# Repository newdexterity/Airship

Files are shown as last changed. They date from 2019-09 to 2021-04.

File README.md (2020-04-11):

# A Low-Cost, Open-Source, Robotic Airship for Education and Research

Miniature indoor robotic airship platforms offer high mobility, safety, and extended flight times. The work focuses on the feasibility, design, development, and evaluation of such a platform for robotics education and research. Selected commercially available envelope materials were considered and tested in terms of their helium retention capability. The obtained envelope properties were used in a feasibility study, demonstrating that indoor airships are environmentally and financially viable, given an appropriate material choice. The platform's mechanical design was studied in terms of gondola placement and rotor angle positioning, resulting in an unconventional, asymmetric arrangement. The developed system was finally tested in a simple path following experiment for proof-of-concept purposes, proving its efficiency in attaining the desired heading and altitude configuration. The proposed robotic airship platform can be used for a variety of education and research oriented applications and its design is open-source facilitating replication by others.

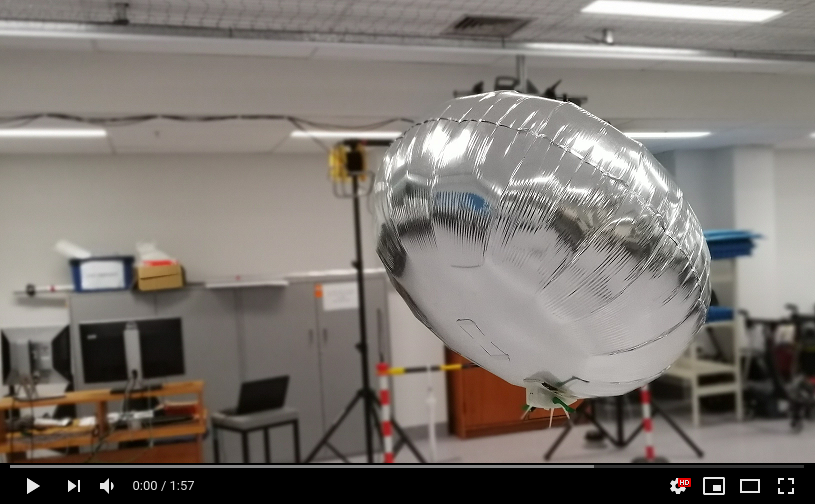
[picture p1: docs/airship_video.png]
Airship video (https://youtu.be/TQCl9RjmE-4)


## Repository Contents
This repository contains the following material:
* Assembly guide and bill of materials
* CAD files of the airship platform
* ROS interface for flight control and path following

## Gondola Design
The airship gondola is built around the electronic components and actuators listed in the provided bill of materials.
The central control and communication unit is a Raspberry Pi Zero W running a Lite version of the Raspbian Stretch operating system. 
Peripheral components include a single cell 500 mAh Li-Ion battery, step-up voltage regulator, motor drivers, three 7x16 mm DC motors, three 57x20 mm propeller units and a camera module that will facilitate the formulation of HRI frameworks.
Rotor speeds can either be controlled by on-board logic or manually via a wireless connection through SSH or an appropriately developed Robot Operating System (ROS) package.
The combined cost of the gondola components (excluding the 3D printing filament and wiring) comes to 90 USD, which drops to 54 USD if the camera module is not required.
The physical frame is 3D printed and built in a modular fashion: the gondola legs and rotor brackets are detachable to facilitate component modification and replacement.
The gondola is attached to the chosen envelope using Velcro.
The assembled gondola and its exploded view model are presented below:
<p align="center">
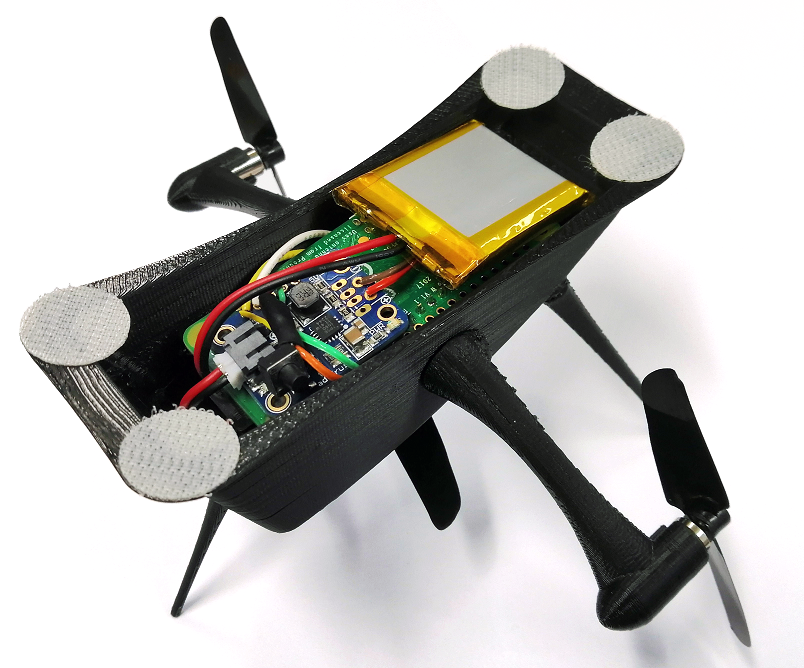
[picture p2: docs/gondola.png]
  
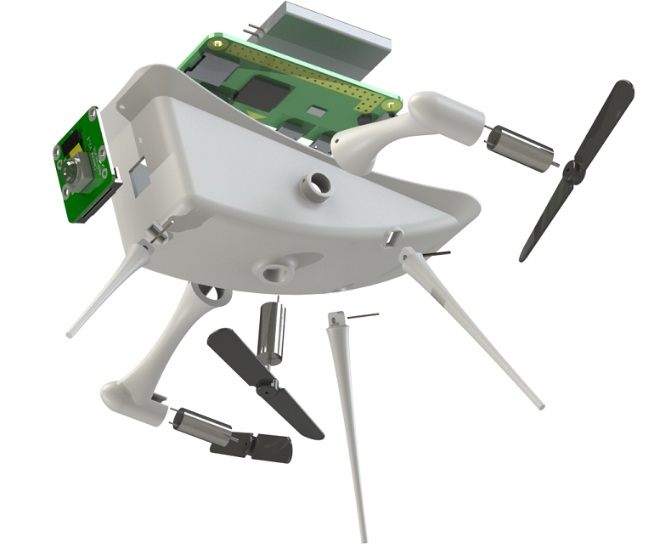
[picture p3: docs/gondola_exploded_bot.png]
  
</p>

## Envelope Material
A number of envelope material candidates were examined with respect to their helium permeability and mechanical properties:
* Qualatex untreated round 41 cm (16 inch) latex balloon
* Qualatex untreated round 61 cm (24 inch) latex balloon
* Qualatex round 61 cm (24 inch) latex balloon treated with Ultra Hi-Float (UHF) \cite{HiFloatPatent}
* Qualatex 61 cm (24 inch) clear Bubble balloon (layered membrane including a high barrier layer of ethylene vinyl alcohol copolymer)
* Qualatex round 91 cm (36 inch) Microfoil (metallised PET) balloon

<p align="center">
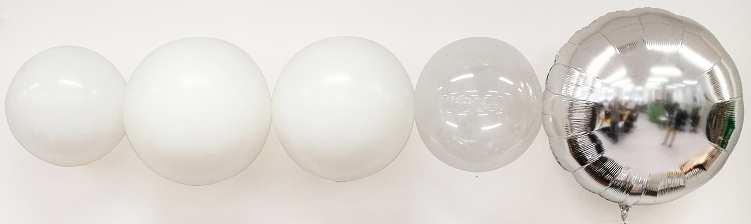
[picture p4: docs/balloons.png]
  
</p>

The daily helium flux through balloon membranes was computed:
<p align="center">
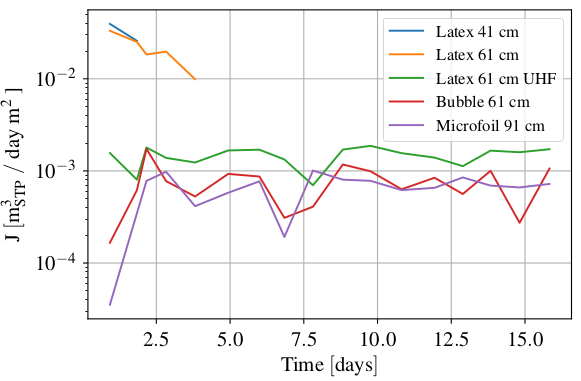
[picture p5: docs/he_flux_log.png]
  
</p>

The average helium flux values and yearly refill costs for different envelope materials:
<p align="center">
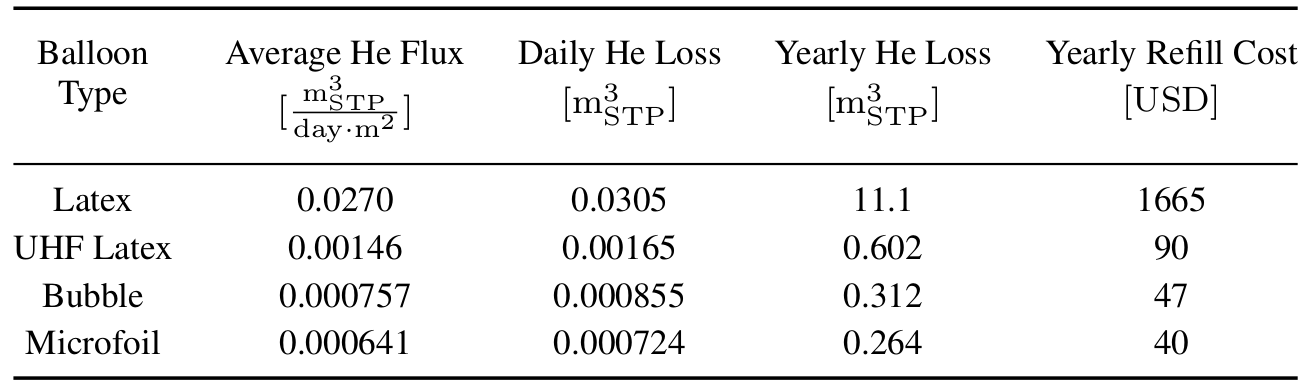
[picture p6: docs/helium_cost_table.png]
  
</p>

The measured mechanical properties of latex, Microfoil and Bubble membranes:
<p align="center">
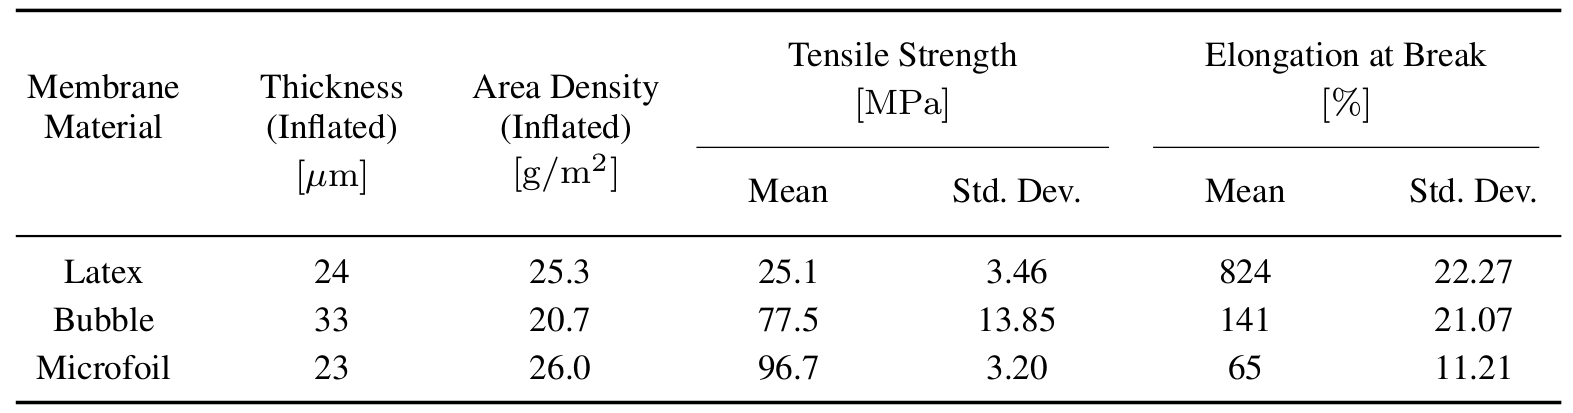
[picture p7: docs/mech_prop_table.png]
  
</p>

## Path Following
The airship was evaluated in terms of its path following ability in an indoor environment.
Path following was implemented using a discrete variation of the carrot-chasing algorithm, where the desired path is segmented into a sequence of waypoints.
In a given location, the airship identifies its position with respect to desired path and directs itself towards an appropriate waypoint:

<p align="center">
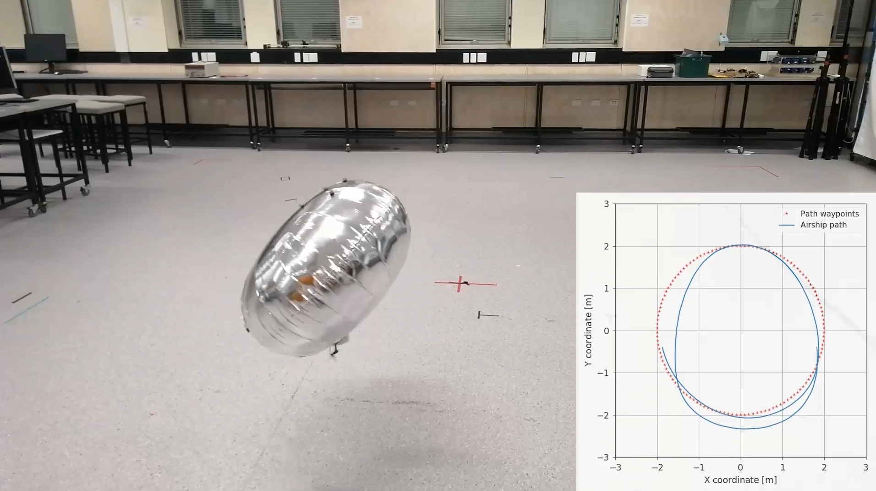
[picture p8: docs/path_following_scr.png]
  
</p>

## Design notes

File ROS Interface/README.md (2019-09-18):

# airshippi_vicon

Example ROS interface to use with the Vicon motion capture system. 
The package relies on the pigpio library: http://abyz.me.uk/rpi/pigpio/ and the vicon_bridge ROS package.

## Usage

The pigpio_setter.py node should be run on the raspberry pi, while others are examples of closed loop flight controllers.

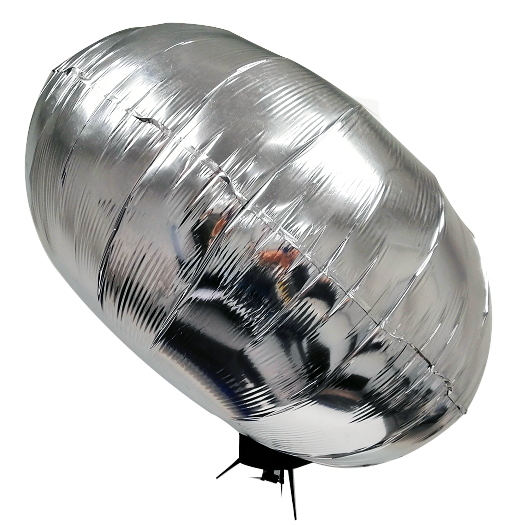
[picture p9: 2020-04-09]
docs/gondola_offset.png

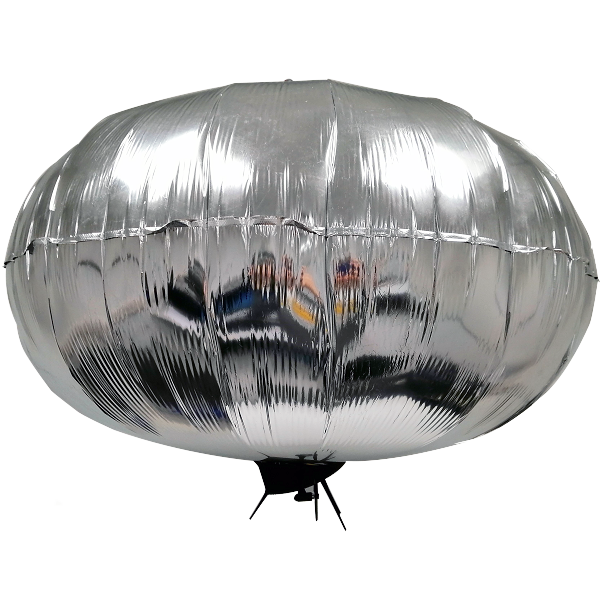
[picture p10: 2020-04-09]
docs/gondola_centred.png

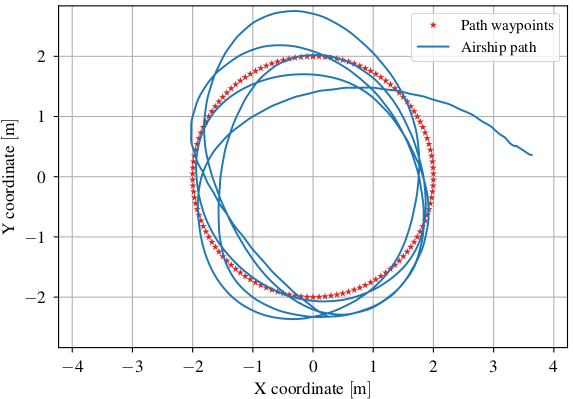
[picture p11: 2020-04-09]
docs/pf_circle.png

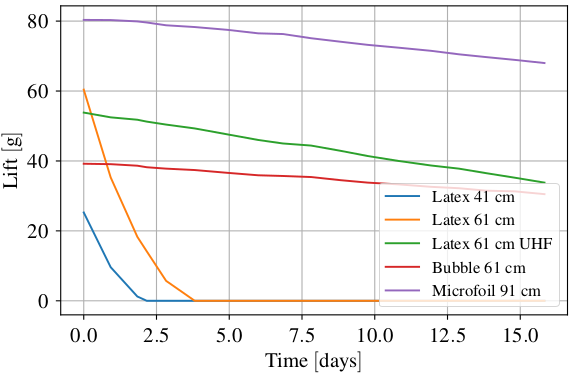
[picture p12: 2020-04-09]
docs/raw_lift.png

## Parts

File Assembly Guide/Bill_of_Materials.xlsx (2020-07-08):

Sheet: USA
PRODUCT NUMBER | DESCRIPTION | QUANTITY | INDIVIDUAL PRICE | COMBINED PRICE | COMPANY | RESELLER COMPANY | LINK TO RESELLER WEBPAGE | ALT LINKS | ADDITIONAL INFO
3400 | Raspberry Pi Zero W | 1 | 10 USD | 10 USD | AdaFruit | AdaFruit | https://www.adafruit.com/product/3400
1578 | Lithium Ion Polymer Battery - 3.7v 500mAh | 1 | 7.95 USD | 7.95 USD | AdaFruit | AdaFruit | https://www.adafruit.com/product/1578
1903 | PowerBoost 500 Basic - 5V USB Boost @ 500mA from 1.8V+ | 1 | 9.95 USD | 9.95 USD | Adafruit | Adafruit | https://www.adafruit.com/product/1903
2135 | DRV8835 Dual Motor Driver Carrier | 1 | 4.49 USD | 4.49 USD | Pololu | Pololu | https://www.pololu.com/product/2135
2990 | DRV8838 Single Brushed DC Motor Driver Carrier | 1 | 3.49 USD | 3.49 USD | Pololu | Pololu | https://www.pololu.com/product/2990
/ | Motor-7x16mm 3.3Ohm w/nanoconnector | 3 | 4.29 USD | 12.87 USD | Plantraco MicroFlight | AliExpress | https://www.aliexpress.com/item/32957638292.html | http://microflight.com/radio-systems/motors/motor-7mm-3-3ohm-w-nanoconnector.html | Micro motor, brushed, width 7mm, length 16.5mm, voltage 3.7 V, resistance 3.3 Ohm
/ | Propeller 57x20 mm | 3 | 1.49 USD | 4.47 USD | Plantraco MicroFlight | Plantraco MicroFlight | http://microflight.com/radio-systems/propellers/prop-57x20-for-1mm-shaft.html
3099 | Raspberry Pi Camera Board v2 - 8 Megapixels | 1 | 29.95 USD | 29.95 USD | AdaFruit | AdaFruit | https://www.adafruit.com/product/3099
3157 | Raspberry Pi Zero v1.3 Camera Cable | 1 | 5.95 USD | 5.95 USD | AdaFruit | AdaFruit | https://www.adafruit.com/product/3157
12683 | Qualatex Round Microfoil Balloon: 36’’ Silver | 1 | ~2.5 USD | ~2.5 USD | Qualatex | Refer to Alt Link | https://us.qualatex.com/en-us/products/12683/?product_type=Qualatex%20Foil%20Balloons | https://us.qualatex.com/en-us/products/12683/?product_type=Qualatex%20Foil%20Balloons

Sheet: Europe
PRODUCT NUMBER | DESCRIPTION | QUANTITY | INDIVIDUAL PRICE | COMBINED PRICE | COMPANY | RESELLER COMPANY | LINK TO RESELLER WEBPAGE | ALT LINK
3400 | Raspberry Pi Zero W | 1 | 10 USD | 10 USD | AdaFruit | AdaFruit | https://www.adafruit.com/product/3400
1578 | Lithium Ion Polymer Battery - 3.7v 500mAh | 1 | 7.95 USD | 7.95 USD | AdaFruit | AdaFruit | https://www.adafruit.com/product/1578
1903 | PowerBoost 500 Basic - 5V USB Boost @ 500mA from 1.8V+ | 1 | 9.95 USD | 9.95 USD | Adafruit | Adafruit | https://www.adafruit.com/product/1903
2135 | DRV8835 Dual Motor Driver Carrier | 1 | 4.49 USD | 4.49 USD | Pololu | Pololu | https://www.pololu.com/product/2135
2990 | DRV8838 Single Brushed DC Motor Driver Carrier | 1 | 3.49 USD | 3.49 USD | Pololu | Pololu | https://www.pololu.com/product/2990
/ | Motor-7mm 3.3Ohm w/nanoconnector | 3 | 4.29 USD | 12.87 USD | Plantraco MicroFlight | Plantraco MicroFlight | http://microflight.com/radio-systems/motors/motor-7mm-3-3ohm-w-nanoconnector.html
/ | Prop-57x20 for 1mm Shaft | 3 | 1.49 USD | 4.47 USD | Plantraco MicroFlight | Plantraco MicroFlight | http://microflight.com/radio-systems/propellers/prop-57x20-for-1mm-shaft.html
3099 | Raspberry Pi Camera Board v2 - 8 Megapixels | 1 | 29.95 USD | 29.95 USD | AdaFruit | AdaFruit | https://www.adafruit.com/product/3099
3157 | Raspberry Pi Zero v1.3 Camera Cable | 1 | 5.95 USD | 5.95 USD | AdaFruit | AdaFruit | https://www.adafruit.com/product/3157
12683 | Qualatex Round Microfoil Balloon: 36’’ Silver | 1 | ~2.5 USD | ~2.5 USD | Qualatex | Refer to Alt Link | https://europe.qualatex.com/en-gb/products/12683/?product_type=Qualatex%20Foil%20Balloons | https://europe.qualatex.com/en-gb/purchase-qualatex-balloons/europe-distributors/

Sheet: Asia
PRODUCT NUMBER | DESCRIPTION | QUANTITY | INDIVIDUAL PRICE | COMBINED PRICE | COMPANY | RESELLER COMPANY | LINK TO RESELLER WEBPAGE | ALT LINK
3400 | Raspberry Pi Zero W | 1 | 10 USD | 10 USD | AdaFruit | AdaFruit | https://www.adafruit.com/product/3400
1578 | Lithium Ion Polymer Battery - 3.7v 500mAh | 1 | 7.95 USD | 7.95 USD | AdaFruit | AdaFruit | https://www.adafruit.com/product/1578
1903 | PowerBoost 500 Basic - 5V USB Boost @ 500mA from 1.8V+ | 1 | 9.95 USD | 9.95 USD | Adafruit | Adafruit | https://www.adafruit.com/product/1903
2135 | DRV8835 Dual Motor Driver Carrier | 1 | 4.49 USD | 4.49 USD | Pololu | Pololu | https://www.pololu.com/product/2135
2990 | DRV8838 Single Brushed DC Motor Driver Carrier | 1 | 3.49 USD | 3.49 USD | Pololu | Pololu | https://www.pololu.com/product/2990
/ | Motor-7mm 3.3Ohm w/nanoconnector | 3 | 4.29 USD | 12.87 USD | Plantraco MicroFlight | Plantraco MicroFlight | http://microflight.com/radio-systems/motors/motor-7mm-3-3ohm-w-nanoconnector.html
/ | Prop-57x20 for 1mm Shaft | 3 | 1.49 USD | 4.47 USD | Plantraco MicroFlight | Plantraco MicroFlight | http://microflight.com/radio-systems/propellers/prop-57x20-for-1mm-shaft.html
3099 | Raspberry Pi Camera Board v2 - 8 Megapixels | 1 | 29.95 USD | 29.95 USD | AdaFruit | AdaFruit | https://www.adafruit.com/product/3099
3157 | Raspberry Pi Zero v1.3 Camera Cable | 1 | 5.95 USD | 5.95 USD | AdaFruit | AdaFruit | https://www.adafruit.com/product/3157
12683 | Qualatex Round Microfoil Balloon: 36’’ Silver | 1 | ~2.5 USD | ~2.5 USD | Qualatex | Refer to Alt Link | https://asia.qualatex.com/en-us/products/12683/?product_type=Qualatex%20Foil%20Balloons | https://asia.qualatex.com/en-us/purchase-qualatex-balloons/asia-distributors/

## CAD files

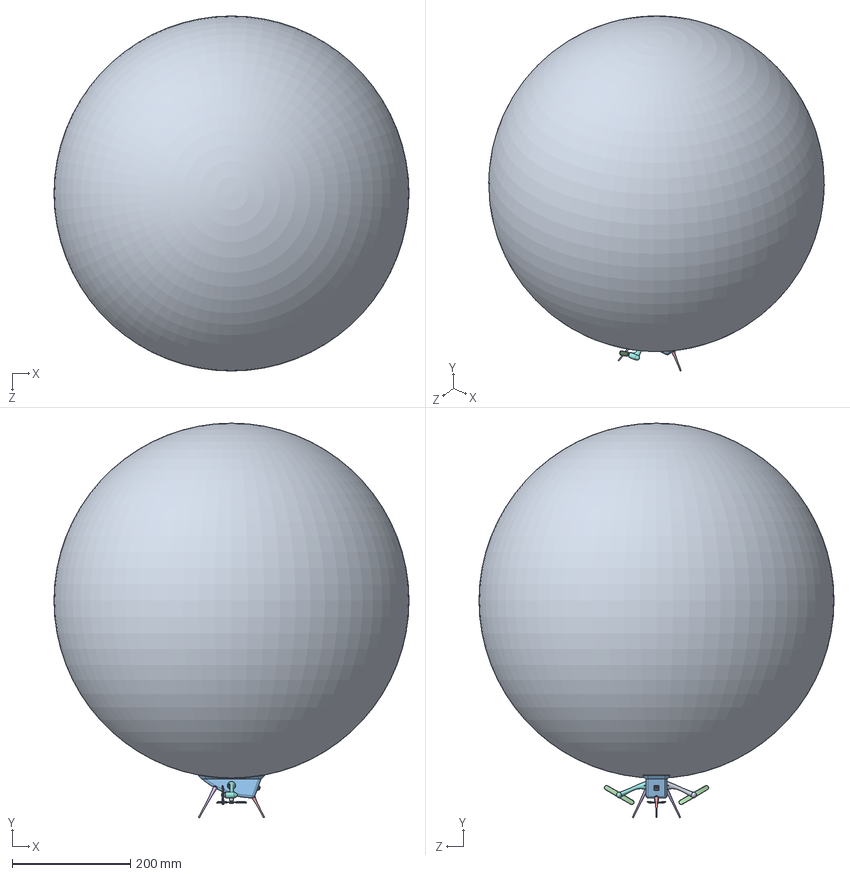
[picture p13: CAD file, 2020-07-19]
CAD/gondola/platform.SLDASM
600.0 x 667.1 x 600.0 mm
RaspberryPiZeroW
PicameraPCB
OVA5647_Housing
OVA5647_Lens_FOV
ribbon_cam
CCD
CAPC-0805-T0.75-BN x 2
CAPC-0402-T0.55-BN x 10
RESC-0402 x 3
RESC-0603 x 2
RESC-1210
c-1-1734248-5-e-raspberry_display
SOT23-5 x 3
KX7 SMD Quartz Crystal Resonator 3.2x2.5mm
c6aaa
4pin_smd x 3
plantraco_7mm_motor x 3
battery_1s_500mah
frame_v3
propeller_57mm x 3
front_leg
back_leg x 2
pinheader_straight x 3
right_wing
left_wing

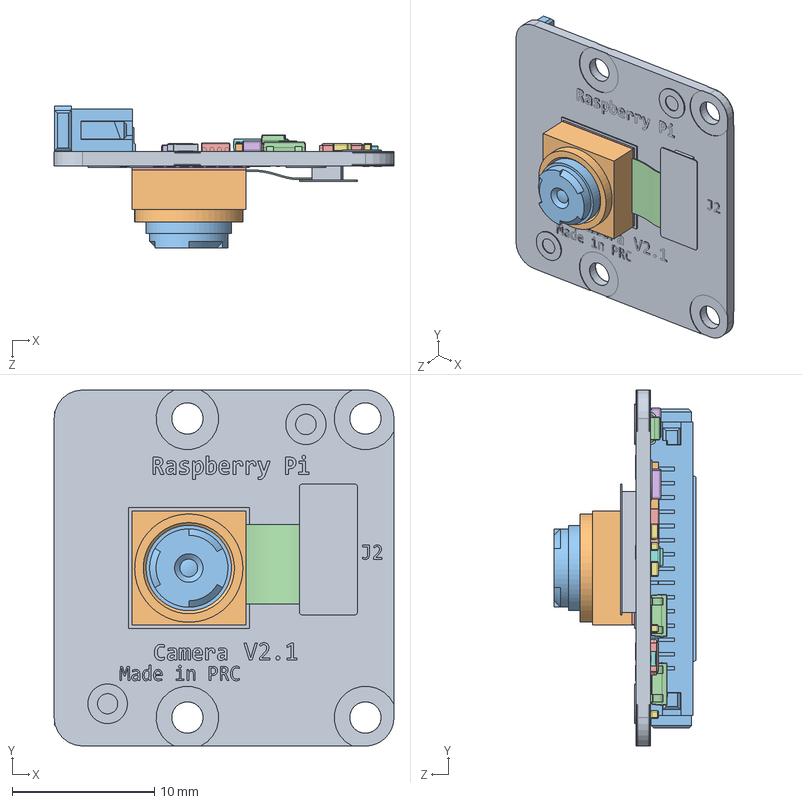
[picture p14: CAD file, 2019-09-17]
CAD/parts/RaspberryPiCameraModuleV2/RspCameraMia.SLDASM
23.9 x 25.0 x 9.96 mm
PicameraPCB
OVA5647_Housing
OVA5647_Lens_FOV
ribbon_cam
CCD
CAPC-0805-T0.75-BN x 2
CAPC-0402-T0.55-BN x 10
RESC-0402 x 3
RESC-0603 x 2
RESC-1210
c-1-1734248-5-e-raspberry_display
SOT23-5 x 3
KX7 SMD Quartz Crystal Resonator 3.2x2.5mm
c6aaa
4pin_smd x 3

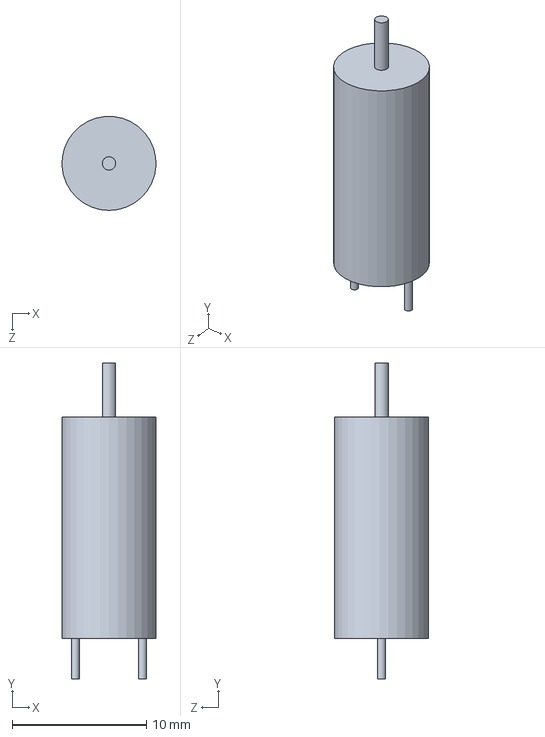
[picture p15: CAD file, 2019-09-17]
CAD/parts/plantraco_7mm_motor.SLDPRT
6.99 x 23.5 x 6.98 mm

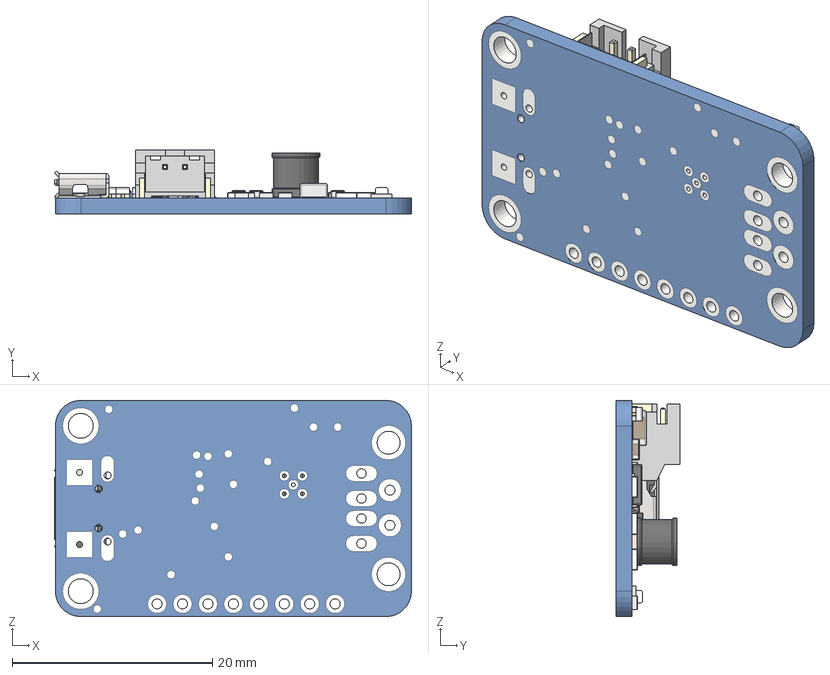
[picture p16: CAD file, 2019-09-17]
CAD/parts/powerboost-500c-1.snapshot.1/PowerBoost 500C v24.step
35.6 x 6.37 x 21.6 mm
MO-229W3030D-1_4000
Molex2pinSMD
RESC-0805 x 14
MicroUSB
CAPC-0805-T0 x 4
LED-0805H1 x 4
pin x 3
TSOP-5 v4
cap
VLC5045

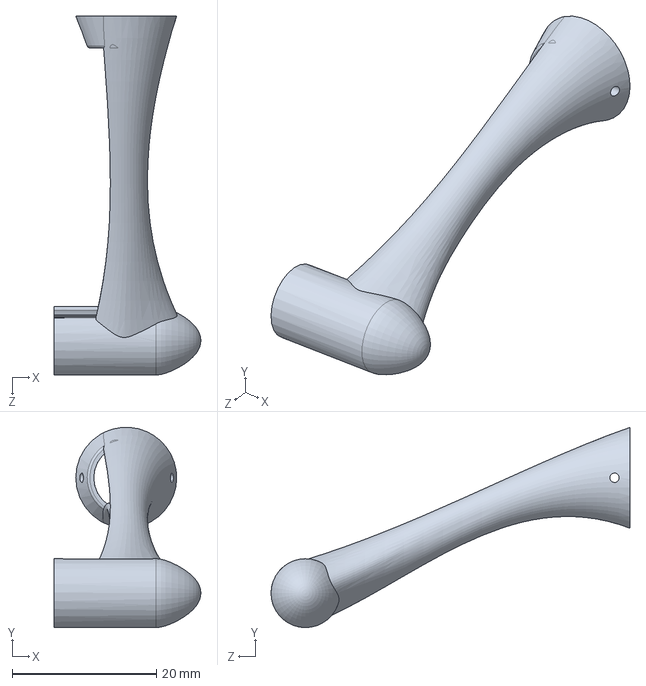
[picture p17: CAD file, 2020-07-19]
CAD/gondola/right_wing.sldprt
20.4 x 27.8 x 49.8 mm

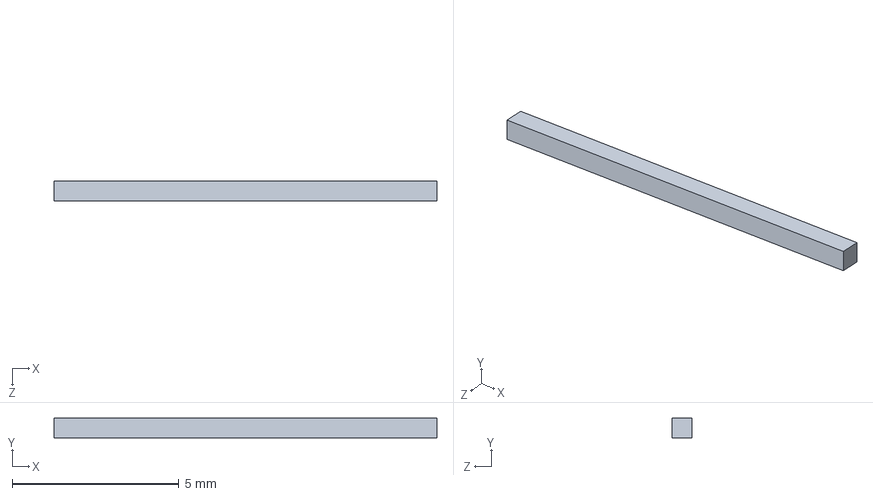
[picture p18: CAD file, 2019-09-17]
CAD/parts/pinheader_straight.SLDPRT
11.5 x 0.6 x 0.6 mm

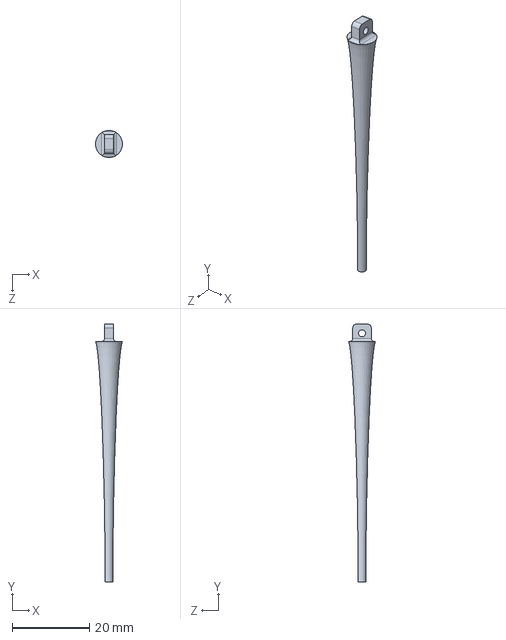
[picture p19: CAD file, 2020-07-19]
CAD/gondola/back_leg.sldprt
6.98 x 66.6 x 6.99 mm

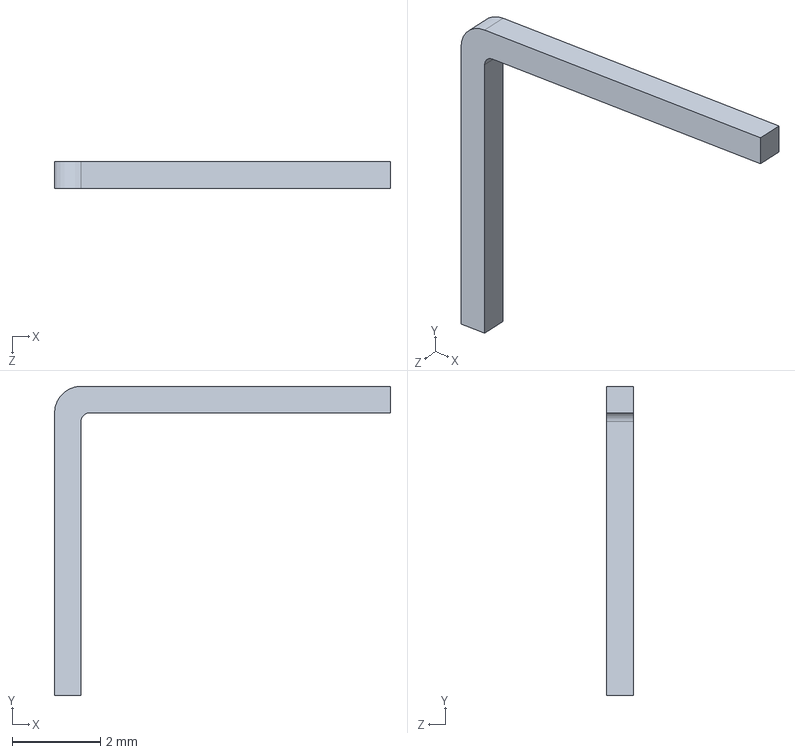
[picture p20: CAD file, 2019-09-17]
CAD/parts/pinheader_bent.SLDPRT
7.60 x 7.00 x 0.6 mm

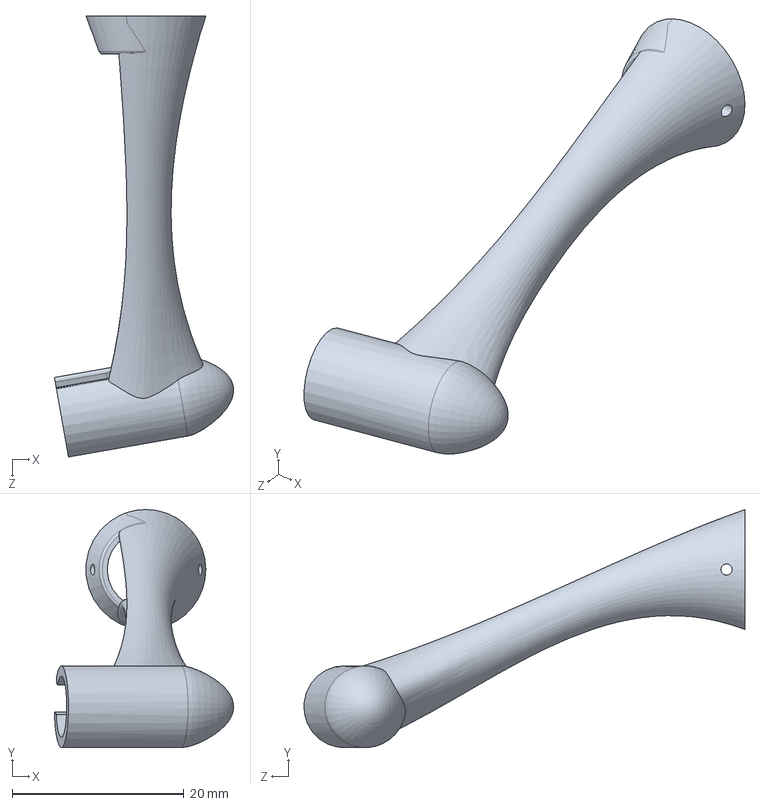
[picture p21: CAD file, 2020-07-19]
CAD/gondola/right_wing_10deg.sldprt
20.9 x 27.8 x 51.4 mm

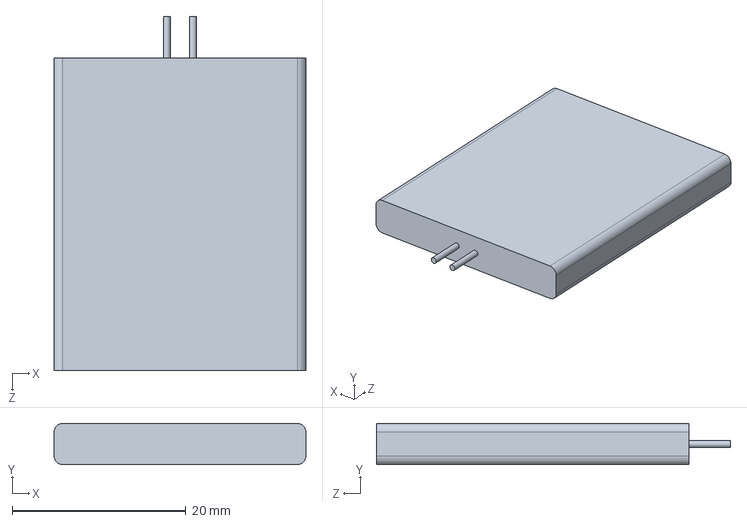
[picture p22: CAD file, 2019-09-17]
CAD/parts/battery_1s_500mah.SLDPRT
29.0 x 4.75 x 40.8 mm

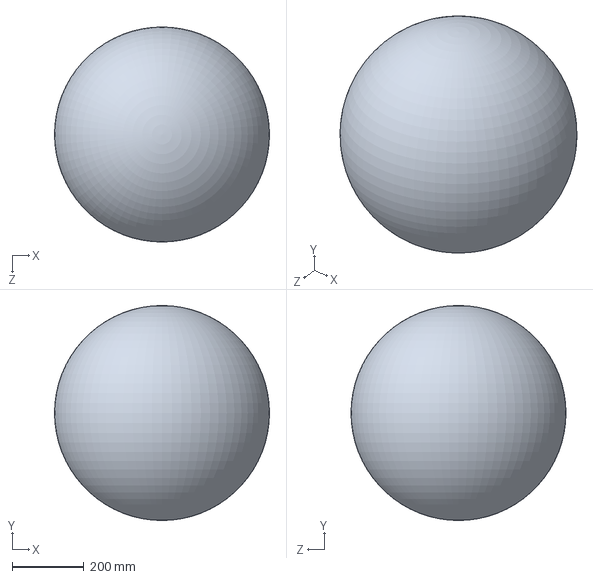
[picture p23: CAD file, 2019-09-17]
CAD/parts/envelope_spherical.SLDPRT
600.0 x 600.0 x 600.0 mm

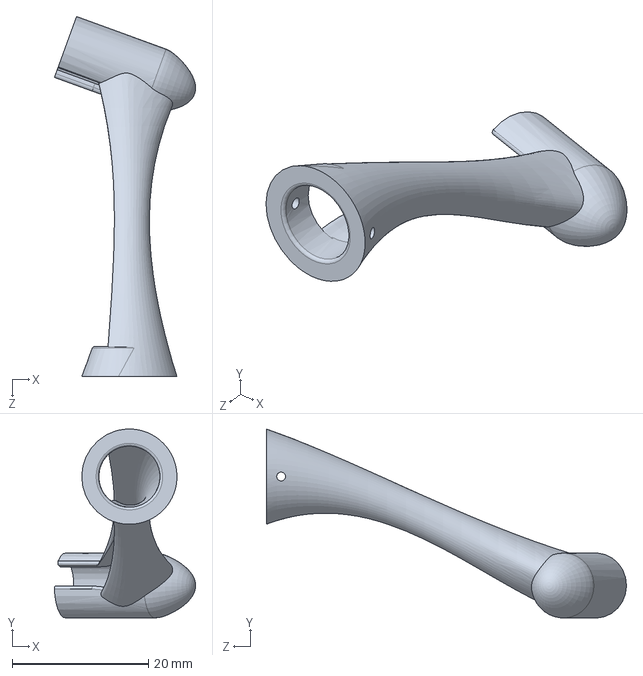
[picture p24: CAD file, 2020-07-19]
CAD/gondola/left_wing_20deg.sldprt
20.8 x 27.8 x 52.9 mm

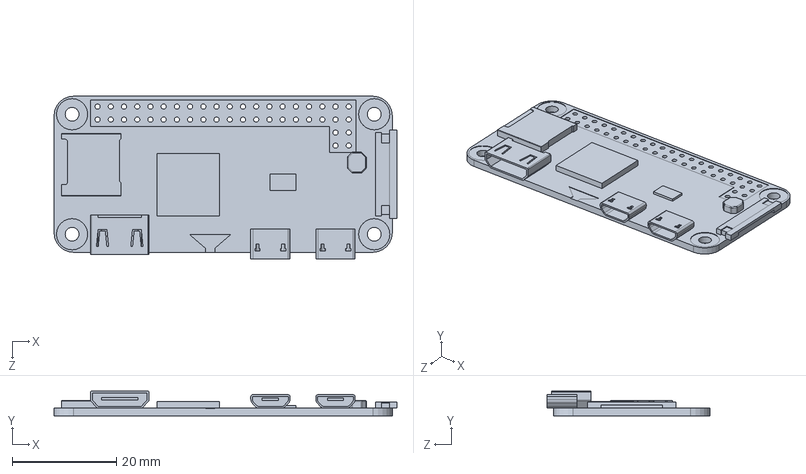
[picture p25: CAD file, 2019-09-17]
CAD/parts/RaspberryPiZeroW.SLDPRT
65.9 x 4.80 x 31.2 mm

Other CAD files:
CAD/parts/RaspberryPiCameraModuleV2/OVA5647_Housing.sldprt
CAD/parts/RaspberryPiCameraModuleV2/CAPC-0805-T0.75-BN.sldprt
CAD/parts/RaspberryPiCameraModuleV2/CCD.sldprt
CAD/gondola/right_wing_5deg.sldprt
CAD/gondola/left_wing.sldprt
CAD/gondola/frame_v3.SLDPRT
CAD/gondola/front_leg.sldprt
CAD/gondola/left_wing_10deg.sldprt
CAD/gondola/left_wing_5deg.sldprt
CAD/gondola/right_wing_20deg.sldprt
CAD/gondola/stl/back_leg.STL
CAD/gondola/stl/frame_v3.STL
CAD/gondola/stl/front_leg.STL
CAD/gondola/stl/left_wing.STL
CAD/gondola/stl/left_wing_10deg.STL
CAD/gondola/stl/left_wing_20deg.STL
CAD/gondola/stl/left_wing_5deg.STL
CAD/gondola/stl/right_wing.STL
CAD/gondola/stl/right_wing_10deg.STL
CAD/gondola/stl/right_wing_20deg.STL
CAD/gondola/stl/right_wing_5deg.STL
CAD/parts/RaspberryPiCameraModuleV2/4pin_smd.sldprt
CAD/parts/RaspberryPiCameraModuleV2/70521906.sldasm
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

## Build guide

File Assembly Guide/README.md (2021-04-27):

# Assembly Guide

## Components
The Bill_of_Materials.xlsx document contains the list of required components to assemble the airship.
It also includes product numbers, prices and links to reseller webpages.

## Motor Driver Connection
The motor drivers can be connected directly to the Raspberry Pi GPIO, as is depicted in the schematic below.
They can be soldered directly to the pins or connected through an appropriate pinheader for easier replacement.
Motor power should be supplied directly from the battery (appropriate pins on the step-up voltage regulator).

<p align="center">
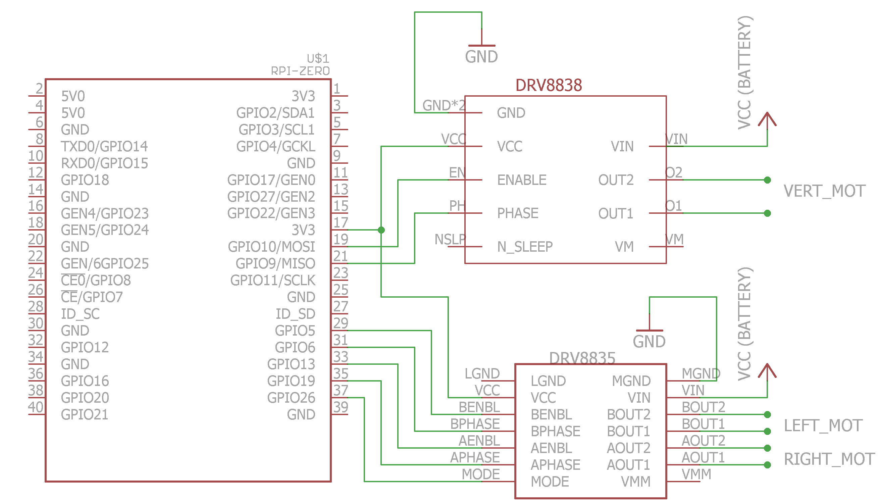
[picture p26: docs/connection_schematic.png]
  
</p>

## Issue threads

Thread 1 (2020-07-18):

Gondola "platform" Solid

marina-go-al, 2020-07-18:
Hello! I am interested in 3d printing the gondola for an educational project using a blimp. However, I have noticed that the "platform" assembly only contains the bottom propeller module and not the ones on the sides (and their corresponding parts/holes), as it appears in the paper. Therefore, I was wondering: could there be something that I am missing?
Thank you very much in advance! (:

gagor15, 2020-07-19:
Hello, thank you for spotting this - some parts were indeed missing.
I've updated the CAD files so everything should be included now: e76559c849d5d8f82b12d201c0d6f98a5627f370

marina-go-al, 2020-07-21:
Perfect, thank you very much, I really appreciate it! Everything looks awesome now

gagor15, 2020-07-21:
Great!

Closed 2020-07-21.

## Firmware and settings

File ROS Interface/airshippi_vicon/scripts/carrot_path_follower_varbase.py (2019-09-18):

#!/usr/bin/env python

## Controls the airship yaw angle

import rospy
import time
import sys
from math import pi, atan2
from geometry_msgs.msg import TransformStamped
from tf.transformations import euler_from_quaternion
from airshippi_vicon.msg import Rotor
from airshippi_vicon.msg import RotorPair
from airshippi_vicon.Path2D import Path, Arc, Line

# ALIGN YAW WITH VICON X AXIS WHEN CREATING OBJECT

# Global params
INVERT_LEFT = True
INVERT_RIGHT = False
RATE_HZ = 5 # Hz
VICON_TOPIC = '/vicon/gal_airship/gal_airship'
#VICON_TOPIC = '/vicon/wand_test/wand_test'

# Carrot
BASE_PWM = 55
P = 55		# Proportional controller gain
VTP_LOOKAHEAD_IDX = 11	# How far ahead the VTP will be placed
PATH_DP = 0.1 		# Distance between path points [m]

# Altitude
target_altitude = 1.8
P_alt = 30
MIN_PWM = 30

# Define path
arc1 = Arc.Arc(start_point=[0, 2], centre=[0, 0], angle=360)
path = Path.Path(segment_list=[arc1], dp=PATH_DP)
#line1 = Line.Line([0,0], [0,4])
#-------------------------------------------
#arc1 = Arc.Arc(start_point=[1, -1], centre=[1, 0], angle=180)
#arc2 = Arc.Arc(start_point=[-1, -1], centre=[-1, 0], angle=-180)
#line1 = Line.Line(arc1.end_point, arc2.start_point)
#line2 = Line.Line(arc2.end_point, arc1.start_point)
#path = Path.Path(segment_list=[arc1, line1, arc2, line2], dp=PATH_DP)

path.reposition(new_centre=[0, 0])

#path.plot()


class CarrotPathFollower(object):
    def __init__(self, path):
	# Parameters
        self.path = path
	self.yaw_target = 0
	self.yaw_current = 0
	self.pos_current = [0, 0, 0]
	self.vtp = [0, 0]
	self.pwm_left = 0
	self.pwm_right = 0
	self.direction_left = 0
	self.direction_right = 0
	self.new_input = True

	self.raw_error = 0
	self.error = 0
	
	# Initialise node
        rospy.init_node('carrot_path_follower', anonymous=True)
	
	# Initialise publisher and subscriber
        self.pub = rospy.Publisher('yaw_rotors', RotorPair, queue_size=1)
        rospy.Subscriber(VICON_TOPIC, TransformStamped, self.callback, queue_size=1)

    def quaternion_to_euler(self, quaternion_vec):
	# Returns [r, p, y] in rad
	rot_q = quaternion_vec
        explicit_quat = [rot_q.x, rot_q.y, rot_q.z, rot_q.w]
        return euler_from_quaternion(explicit_quat)

    def get_yaw_target(self, current_pos_x, current_pos_y):
	# Generate current_pos
	current_pos = [current_pos_x, current_pos_y]
	
	# Get closest point on path
	closest_idx = self.path.get_closest(current_pos)

	# Get VTP
	self.vtp = self.path.get_point(closest_idx + VTP_LOOKAHEAD_IDX)

	# Get angle between the Virtual Target Point and current position, wrt the x axis
	vtp_angle = atan2(self.vtp[1] - current_pos[1], self.vtp[0] - current_pos[0])
	
	return vtp_angle


    def callback(self, data):
        # Get yaw as the third element in the euler angle vector
        self.yaw_current = self.quaternion_to_euler(data.transform.rotation)[2]

	# Get current position
	self.pos_current = data.transform.translation
	
	# Get error
	self.yaw_target = self.get_yaw_target(self.pos_current.x, self.pos_current.y)
	error = self.yaw_target - self.yaw_current
	
	self.raw_error = error
	# Handle angle wrapping
	if error > pi:
	    error -= 2*pi
	elif error < -pi:
	    error += 2*pi
	self.error = error

	# Get shift from the base pwm	
	pwm_shift = -P*error

	# Get Base pwm depending on altitude, but no lower than base
	base_pwm_mod = BASE_PWM + P_alt*(target_altitude - self.pos_current.z)
	#if base_pwm_mod < BASE_PWM:
	#   base_pwm_mod = BASE_PWM

	# Get raw pwm
	left_pwm = base_pwm_mod + pwm_shift
	right_pwm = base_pwm_mod - pwm_shift

	# Save pwm and direction for left
	self.direction_left = int((left_pwm < 0) != INVERT_LEFT)
	left_pwm = abs(left_pwm)
	self.pwm_left = max(MIN_PWM, min(left_pwm, 255))

	# Save pwm and direction for right
	self.direction_right = int((right_pwm < 0) != INVERT_RIGHT)
	right_pwm = abs(right_pwm)
	self.pwm_right = max(MIN_PWM, min(right_pwm, 255))

	# Note the new input
	self.new_input = True

        # Log it
        #rospy.loginfo(rospy.get_caller_id() + '\nAltitude: %s, Target: %s, Thruster value: %s', z, self.z_target, self.pwm_out)

    def run(self):
	# Set rate
        rate = rospy.Rate(RATE_HZ)
        while not rospy.is_shutdown():
	    # Construct Rotor and publish it only if a new input was received in the time since the last publish
	    if self.new_input:
                left = Rotor(pwm=self.pwm_left, direction=self.direction_left)
		right = Rotor(pwm=self.pwm_right, direction=self.direction_right)
		self.new_input = False
	    else:
		left = Rotor(pwm=0, direction=0)
		right = Rotor(pwm=0, direction=0)
            self.pub.publish(left, right)
	    rospy.loginfo("\nYaw: %s, Target: %s, Left: %s, Right: %s", self.yaw_current, self.yaw_target, left, right)
	    rospy.loginfo("\nCurrent_pos: %s, VTP: %s", self.pos_current, self.vtp)
	    rospy.loginfo("\nRaw error: %s, Modified error: %s", self.raw_error, self.error)
            rate.sleep()

def usage():
    return "%s yaw_target"%sys.argv[0]


if __name__ == '__main__':
    print("Starting carrot path follower.")
    cpf = CarrotPathFollower(path)
    cpf.run()

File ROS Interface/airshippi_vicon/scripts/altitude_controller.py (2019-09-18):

#!/usr/bin/env python

## Controls the airship altitude

import rospy
import time
import sys
from geometry_msgs.msg import TransformStamped
from airshippi_vicon.msg import Rotor
#from airshippi_vicon import testmodule

# Global params
P = 90
I = 0.5
D = 0
RATE_HZ = 5 # Hz
VICON_TOPIC = '/vicon/gal_airship/gal_airship'
#VICON_TOPIC = '/vicon/wand_test/wand_test'

class AltitudeController(object):
    def __init__(self, z_target=0):
	# Variables
        self.z_target = z_target
	self.z_current = 0
	self.pwm_out = 0
	self.direction_out = 0
	self.new_input = True
	self.integral = 0
	self.last_error = 0
	
	# Initialise node
        rospy.init_node('altitude_controller', anonymous=True)
	
	# Initialise publisher and subscriber
        self.pub = rospy.Publisher('altitude_rotor', Rotor, queue_size=1)
        rospy.Subscriber(VICON_TOPIC, TransformStamped, self.callback, queue_size=1)

    def callback(self, data):
        # Get vertical position
        self.z_current = data.transform.translation.z

	# Get error
	error = self.z_target - self.z_current

	# Get integral
	self.integral += error/RATE_HZ

	# Get derivative
	derivative = (error - self.last_error)*RATE_HZ

        # Get raw motor value
        raw_pwm = -(P*error + I*self.integral + D*derivative)

	# Save pwm and direction
	self.direction_out = int(raw_pwm > 0)
	raw_pwm = abs(raw_pwm)
	self.pwm_out = max(0, min(raw_pwm, 255))
	
	# Note the new input
	self.new_input = True

	# Update error
	self.last_error = error	

        # Log it
        #rospy.loginfo(rospy.get_caller_id() + '\nAltitude: %s, Target: %s, Thruster value: %s', z, self.z_target, self.pwm_out)

    def run(self):
	# Set rate
        rate = rospy.Rate(RATE_HZ)
        while not rospy.is_shutdown():
	    # Construct Rotor and publish it only if a new input was received in the time since the last publish
	    if self.new_input:
                rotor = Rotor(pwm=self.pwm_out, direction=self.direction_out)
		self.new_input = False
	    else:
		rotor = Rotor(pwm=0, direction=0)
            self.pub.publish(rotor)
	    rospy.loginfo("\nAltitude: %s, Target: %s, Thruster value: %s", self.z_current, self.z_target, rotor)
            rate.sleep()

def usage():
    return "%s z_target"%sys.argv[0]


if __name__ == '__main__':
    if len(sys.argv) == 2:
        z_target = float(sys.argv[1])
    else:
        print(usage())
        sys.exit(1)
    print("Setting desired altitude to %s"%(z_target))
    ac = AltitudeController(z_target)
    ac.run()

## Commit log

2019-09-17 Include airhip CAD model
    [1050281001.sldasm, 4pin_smd.sldprt, 595492200.sldasm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]
2020-01-23 Add bill of materials
    [Bill_of_Materials.xlsx]
2020-04-06 Update BOM with regional data
    [Bill_of_Materials.xlsx]
2020-04-07 Remove extra CAD files
    [1050281001.sldasm, 595492200.sldasm, 603290992.sldasm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]
2020-07-08 Update motor reseller
    [Bill_of_Materials.xlsx]
2020-07-19 Update gondola CAD files
    [back_leg.STL, back_leg.sldprt, bracket_detached.SLDPRT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]
2021-04-27 Add connection schematic
2021-04-27 Update assembly guide
